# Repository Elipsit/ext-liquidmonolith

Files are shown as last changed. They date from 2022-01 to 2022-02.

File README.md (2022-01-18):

# ext-liquidmonolith
**Burning Man 2022; Project Liquid Monolith**
## Project Description
The Liquid Monolith invites participants to see the world through different lenses, by presenting them with a fluid moving display that resembles "Rorschach Inkblot Tests" that helps us unravel their dreams.<br/>

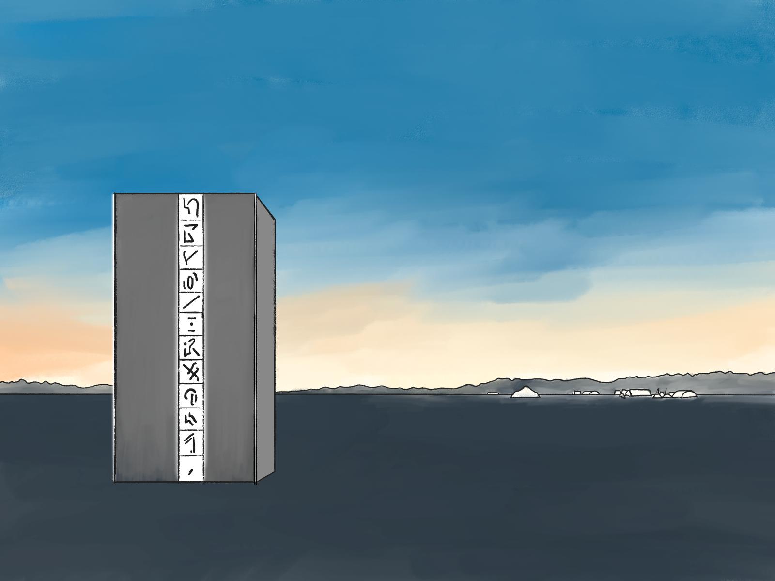
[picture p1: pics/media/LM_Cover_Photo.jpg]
LM_Cover_Photo


### Current Status
This project is in a prototype development stage<br/>

# Working Pototype
**Here is a working prototype of electromagnets sequencing the ferrofluid in the display panel:**

The 16 coil demo next to the large sample tank<br/>
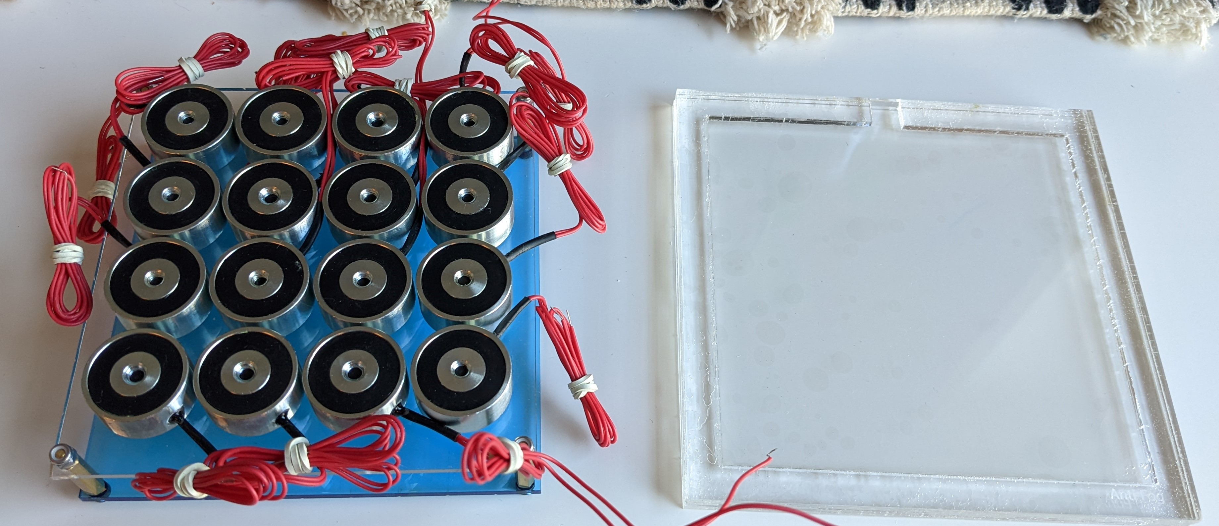
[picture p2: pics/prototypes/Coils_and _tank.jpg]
coil_and_tank


Here is a working demo<br/>

Demo_16_Array (https://www.youtube.com/watch?v=od863sYBf_k)

## Youtube Videos
**This is a link to the playlist of testing videos:**<br/>
https://youtube.com/playlist?list=PLEcu0RNHthJt5TEQliIqUSDUa66y-6SBE

# Project Research
This project was inspired from a youtube channel called [Applied Procrastination](https://www.youtube.com/watch?v=5PFgVtzsXHM)

# The Prototype

## Electrical
Several electromagnet coil topologies were tested:<br/>
Coil_options

I ordered a sample ferrofluid vial and used a custom PCB from a previous project to validate coils<br/>

Demo_single (https://www.youtube.com/watch?v=ZpuwwRlafGQ)

I chose to settle of a smaller one that was cheaper. A smaller coil required a system voltage increase from 12V to 24V to maintain the needed force.<br/>

Here is our prototype 16 coil array:<br/>

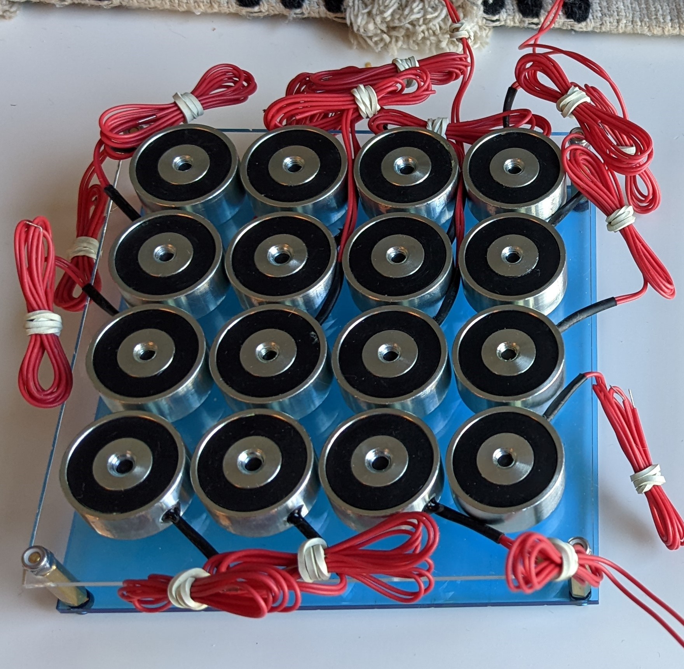
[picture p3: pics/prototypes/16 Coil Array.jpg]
16_Coil_Array

I made a custom board to test the coils <br/>

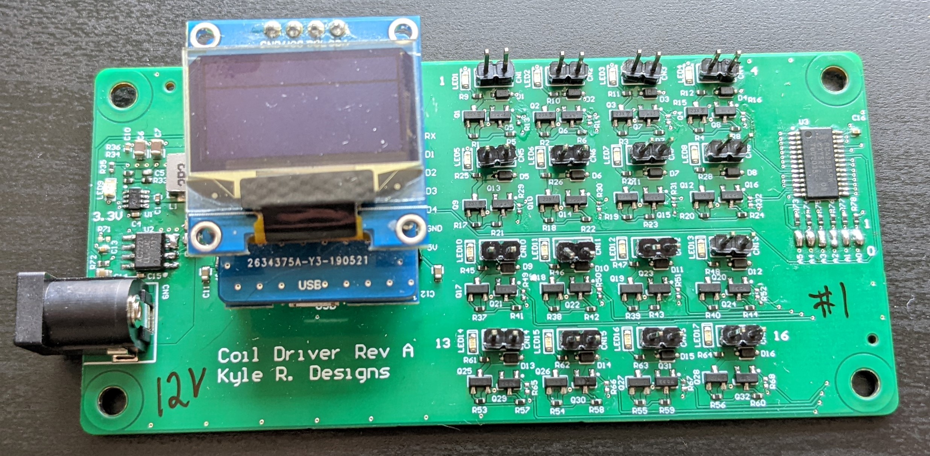
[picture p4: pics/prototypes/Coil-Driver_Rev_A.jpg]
Driver_RevA


Here is a video of the start up test:<br/>
PWM_Driver (https://www.youtube.com/watch?v=yCkvBs--dNo)

## Ferrofluid Tank

### Tank Materials

The demo video from [Applied Procrastination](https://www.youtube.com/watch?v=5PFgVtzsXHM) used glass enclosures, but I felt this would be an issue for the Playa.
I chose to research into Acrylic tanks. This was an issues since Ferrofluid is sticky and tends to coat most materials.
Research was done into anti-stick coatings.

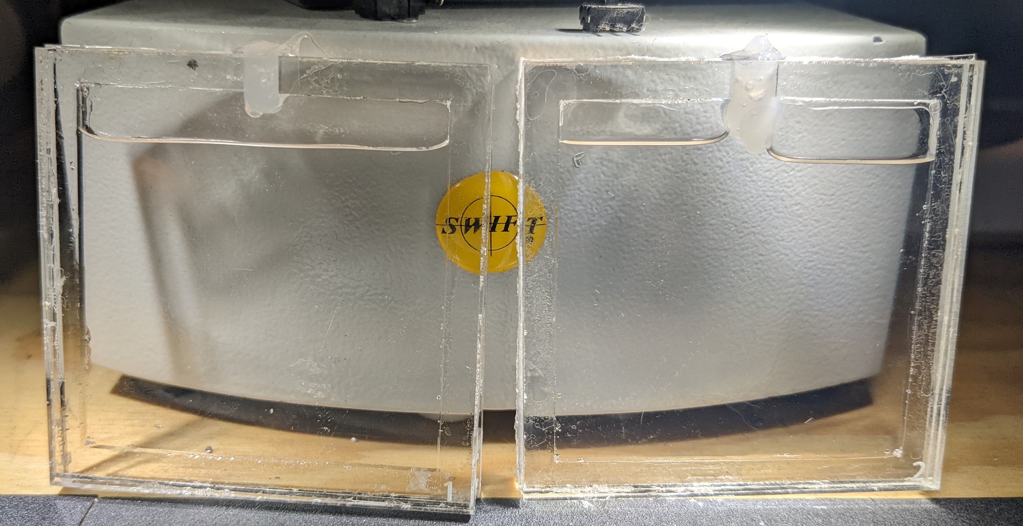
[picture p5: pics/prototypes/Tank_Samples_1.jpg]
Tank_Samples1


Some coatings perfromed better than others:<br/>

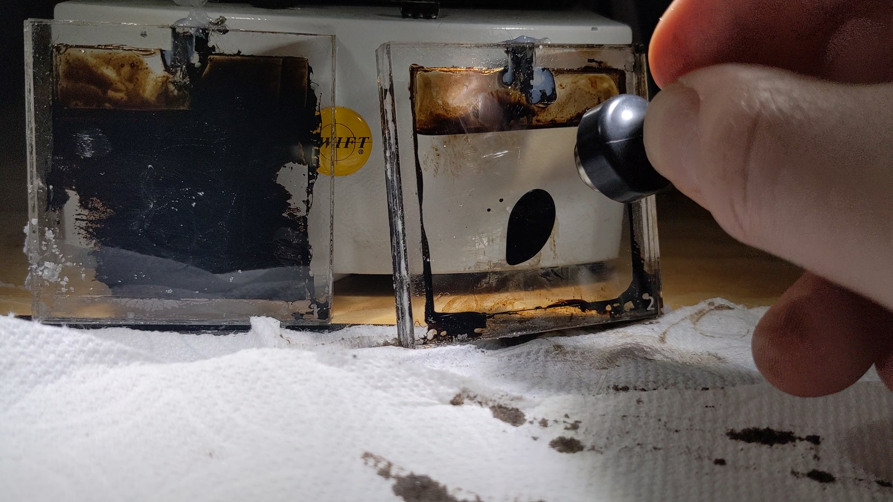
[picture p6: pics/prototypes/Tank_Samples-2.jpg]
Tank_Samples2

			
Here is a video of testing:<br/>
			
Sample_tank (https://www.youtube.com/watch?v=bsLCswysqHQ)

several glue and epoxy options were tested before a water tight solution was found:<br/>

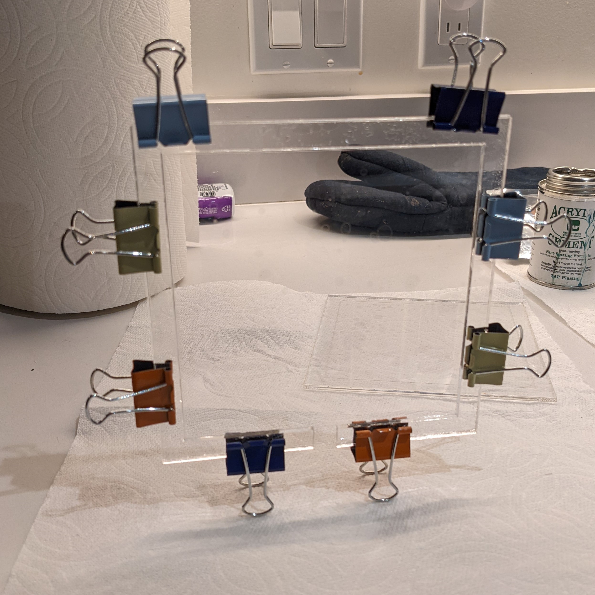
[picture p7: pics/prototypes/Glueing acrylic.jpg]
gluing


When I was able to build one that perfromed as well as the glass ones I scaled the size to fit the 16 electromagnet demo<br/>

large-tank

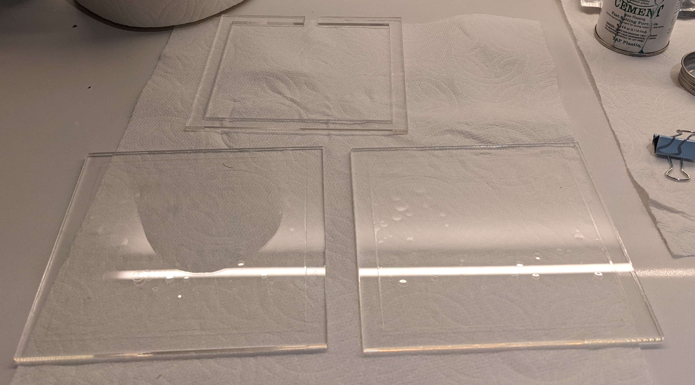
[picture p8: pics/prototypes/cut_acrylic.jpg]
Cut_Acrylic


Here is the completed tank<br/>

Completed_large_tank

Here is a Video:<br/>
Demo_Tank (https://www.youtube.com/watch?v=9LUUrNeGJJY)

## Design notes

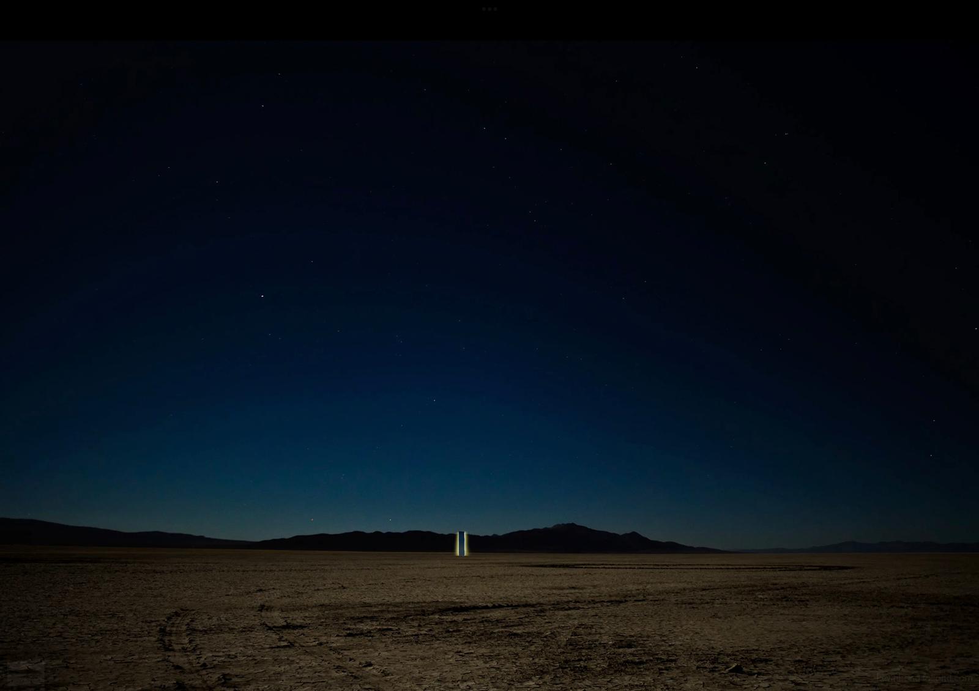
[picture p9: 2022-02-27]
pics/media/WhatsApp Image 2022-01-17 at 5.41.11 PM.jpeg

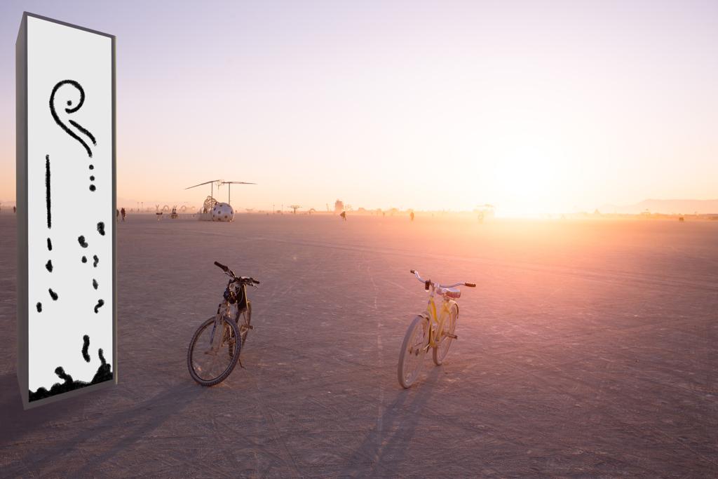
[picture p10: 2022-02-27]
pics/media/LM_Day.jpeg

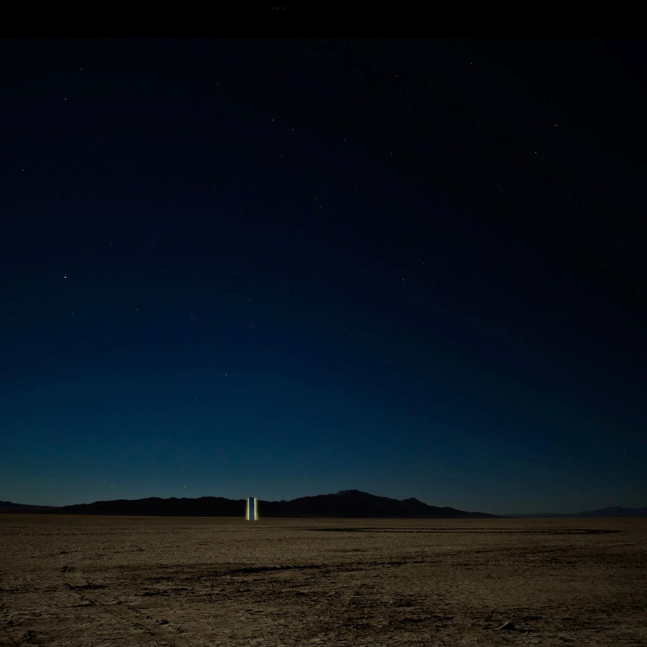
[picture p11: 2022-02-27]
pics/media/WhatsApp Image 2022-01-17 at 5.41.17 PM.jpeg

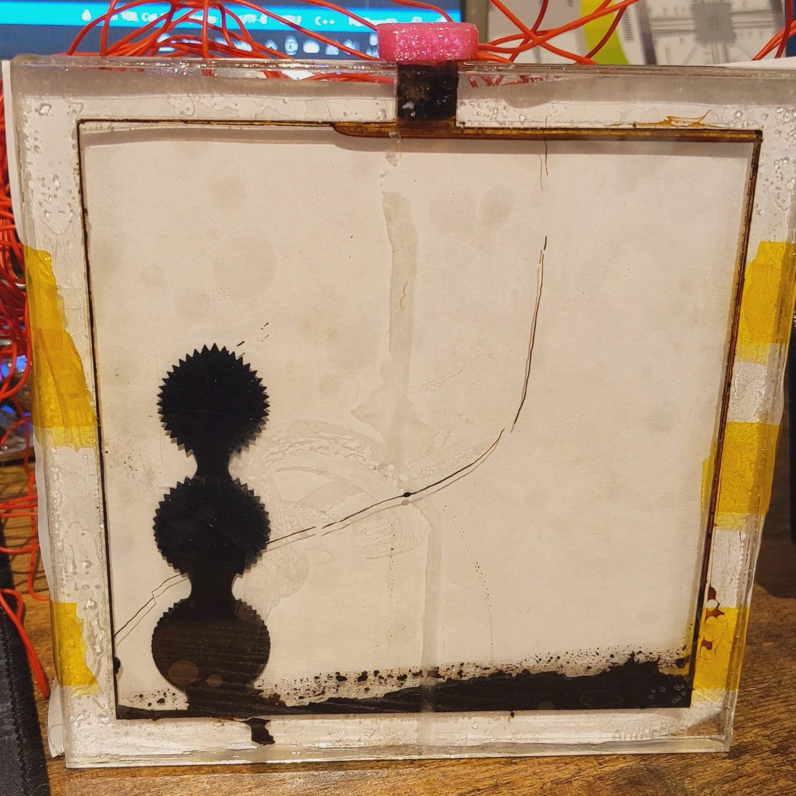
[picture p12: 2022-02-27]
pics/prototypes/3Coil-demo.jpg

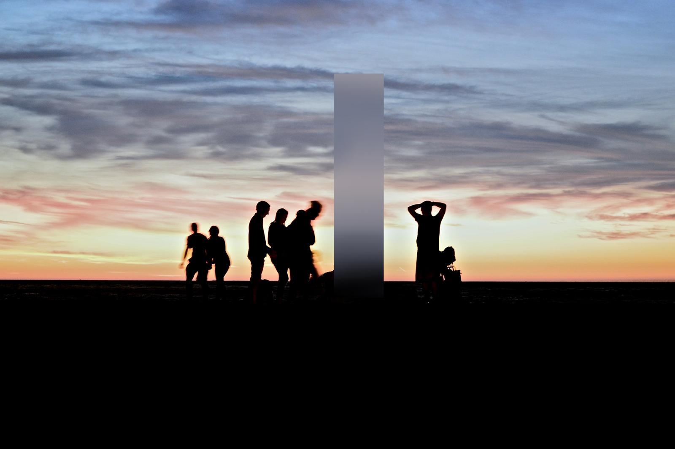
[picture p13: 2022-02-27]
pics/media/LM_Sunset.jpeg

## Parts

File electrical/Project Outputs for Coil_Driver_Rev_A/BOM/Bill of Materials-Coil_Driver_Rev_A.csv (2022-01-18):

Description | Designator | Footprint | Quantity | Manufacturer 1 | Manufacturer Part Number 1 | Supplier 1 | Supplier Part Number 1
±10% 16V Ceramic Capacitor X5R 0402 (1005 Metric) | C1, C4, C10 | CAPC0402(1005)_L | 3 | Murata | GRM155R61H104KE19D | Digi-Key | 490-11917-1-ND
4.99K 0402 | R69, R70 | RESC0402(1005)_N | 2 | Panasonic | ERJ-2RKF4991X | Digi-Key | P4.99KLCT-ND
10 kOhms ±0.1% 0.063W, 1/16W Chip Resistor 0402 (1005 Metric) Automotive AEC-Q200 Thin Film | R1, R2, R3, R4, R5, R6, R7, R8, R13, R14, R15, R16, R17, R18, R19, R20, R21, R22, R23, R24, R29, R30, R31, R32, R37, R38, R39, R40, R41, R42, R43, R44, R49, R50, R51, R52, R53, R54, R55, R56, R57, R58, R59, R60, R65, R66, R67, R68, R73, R74, R75, R76, R77, R78 | RESC0402(1005)_L | 54 | Stackpole Electronics | RNCF0402BTE10K0 | Digi-Key | RNCF0402BTE10K0CT-ND
10µF ±10% 10V Ceramic Capacitor X7R 0805 (2012 Metric) | C2, C3, C6, C7 | CAPC0805(2012)_L | 4 | Murata | GRM21BR71A106KA73K | Digi-Key | 490-14381-1-ND
47pF ±5% 25V Ceramic Capacitor C0G, NP0 0402 (1005 Metric) | C5 | CAPC0402(1005)_L | 1 | KEMET | C0402C470J3GACTU | Digi-Key | 399-C0402C470J3GAC7867CT-ND
90.9 kOhms ±1% 0.063W, 1/16W Chip Resistor 0402 (1005 Metric) Automotive AEC-Q200 Thick Film | R33 | RESC0402(1005)_L | 1 | Stackpole Electronics | RMCF0402FT90K9 | Digi-Key | RMCF0402FT90K9CT-ND
CAP CER 0.1UF 16v X7R 0402 | C15, C16 | CAPC0402(1005)_L | 2 | Taiyo Yuden | EMK105BJ104KV-F | Digi-Key | 587-1226-1-ND
CAP CER 4.7uF 16V X5R 0603 | C11, C12 | CAPC0603(1608)_L | 2 | TDK | C1608X5R1C475K080AC | Digi-Key | 445-7478-1-ND
CAP CER 4700PF 50V X7R 0402 | C13 | CAPC0402(1005)_N | 1 | Murata | GRM155R71H472KA01J | Digi-Key | 490-8259-1-ND
CONN JACK R/A PCB 5.5X2.5MM | CN9 | 54-00130 | 1 | Tensility | 54-00130 | Digi-Key | 839-1513-ND
Current Sensor 5A 1 Channel Hall Effect, Differential Bidirectional | U2 | SOG.050/8A | 1 | Allegro MicroSystems | ACS725LLCTR-05AB-T
DIODE ZENER 13V 250MW SOD323 | D1, D2, D3, D4, D5, D6, D7, D8, D9, D10, D11, D12, D13, D14, D15, D16 | SOD-323 | 16 | Central Semiconductor | CMDZ5243B TR PBFREE | Digi-Key | 1514-CMDZ5243BTRPBFREECT-ND
FIXED IND 3.3UH 5A 54.7 MOHM SMD | L1 | INDP5252X30N | 1 | Vishay Dale | IHLP2020CZER3R3M01 | Digi-Key | 541-1269-1-ND
Header, 2-Pin | CN1, CN2, CN3, CN4, CN5, CN6, CN7, CN8, CN10, CN11, CN12, CN13, CN14, CN15, CN16, CN17 | HDR1X2 | 16 | TE Connectivity | 826936-2 | Digi-Key | A122912-ND
IC LED DRVR LIN DIM 25MA 28TSSOP / LED Driver 10000uA Supply Current 28-Pin TSSOP | U3 | TSOP65P640X110-28N | 1 | NXP Semiconductors | PCA9685PW
IC REG BUCK ADJ 4A TSOT23-8 | U1 | TSOT-23-8 | 1 | Richtek | RT6254AHGJ8F | Digi-Key | RT6254AHGJ8FCT-ND
LED GREEN CLEAR THIN 0603 SMD | LED1, LED2, LED3, LED4, LED5, LED6, LED7, LED8, LED10, LED11, LED12, LED13, LED14, LED15, LED16, LED17 | SM-LED-0603 | 16 | Vishay Lite-On | LTST-C191TGKT | Digi-Key | 160-1888-1-ND
LED GREEN CLEAR THIN 0603 SMD | LED9 | SM-LED-0603 | 1 | Vishay Lite-On | LTST-C191TGKT | Digi-Key | 160-1888-1-ND
MOSFET N-CH 60V 0.36A SOT-23 | Q5, Q6, Q7, Q8, Q13, Q14, Q15, Q16, Q21, Q22, Q23, Q24, Q29, Q30, Q31, Q32 | SOT23-3L | 16 | ON Semiconductor | 2V7002LT1G
MOSFET P-CH 20V 4.2A SOT23 | Q1, Q2, Q3, Q4, Q9, Q10, Q11, Q12, Q17, Q18, Q19, Q20, Q25, Q26, Q27, Q28 | DMG2305UX-7 | 16 | Rohm | RQ5C035BCTCL | Digi-Key | RQ5C035BCTCLCT-ND
PREFERRED (<3.3V): CAP CER 1UF 10V X7R 0603 | C14 | CAPC0603(1608)_L | 1 | KEMET | C0603C105K8RACTU | Digi-Key | 399-C0603C105K8RAC7867TR-ND
RES 1K OHM 1% 1/16W 0402 | R72 | RESC0402(1005)_N | 1 | Stackpole Electronics | RMCF0402FT1K00 | Digi-Key | RMCF0402FT1K00CT-ND
RES 20K OHM 1% 1/10W 0402 | R36 | RESC0402(1005)_L | 1 | Stackpole Electronics | RMCF0402FT20K0 | Digi-Key | RMCF0402FT20K0CT-ND
RES SMD 4.99K OHM 1% 1/16W 0402 | R34 | RESC0402(1005)_L | 1 | Samsung | RC1005F4991CS | Digi-Key | 1276-3468-1-ND
RES SMD 5.1K OHM 1% 1/10W 0402 | R9, R10, R11, R12, R25, R26, R27, R28, R45, R46, R47, R48, R61, R62, R63, R64 | RESC0402(1005)_L | 16 | Panasonic | ERJ-2RKF5101X | Digi-Key | P5.10KLCT-ND
RES SMD 330 OHM 1% 1/10W 0402 | R35 | RESC0402(1005)_L | 1 | Panasonic | ERJ-U02F3300X | Digi-Key | 10-ERJ-U02F3300XCT-ND
Solderable jumper for connecting things | J1, J2, J3, J4, J5, J6, J7 | RESC0603(1608)_L | 7
Wemo Mini Shield for ESP-12 | CN18 | Wemos_d1 | 1

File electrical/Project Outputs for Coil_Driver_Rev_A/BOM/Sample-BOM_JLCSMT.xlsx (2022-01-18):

Comment | Designator | Footprint | JLCPCB Part #（optional）
100uF | C1 | CAP-SMD_L3.5-W2.8 | C16133
15K | R5,R6 | R0603 | C22809
DC-005-20A_C136744 | DC1 | DC-IN-TH_DC-005-20A | C136744
Header-Female-2.54_1x8 | P2,P3 | HDR-TH_8P-P2.54-V | C27438
K2-1102DP-C4SW-04 | SW1 | KEY-TH_4P-L6.0-W6.0-P4.50-LS6.5 | C110153
ATMEGA328P-PU | U1 | DIP-28_L34.6-W7.3-P2.54-LS10.2-BL | C33901
670688000 | USB1 | USB-B-TH_67068-8000 | C114097

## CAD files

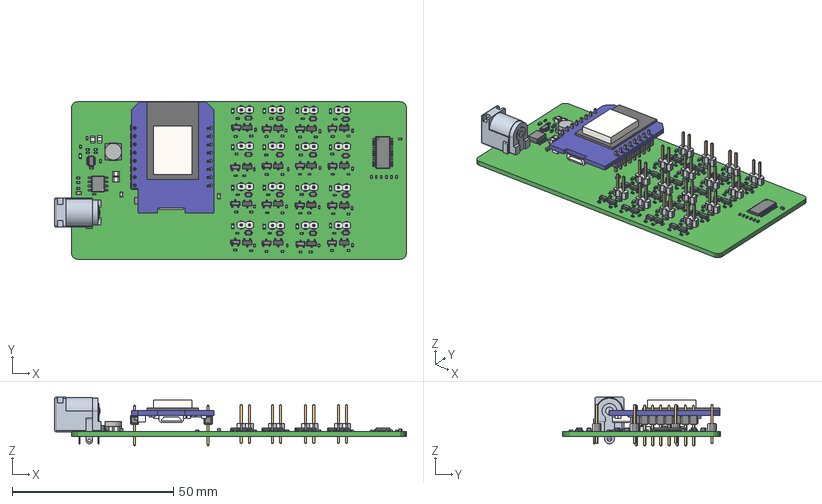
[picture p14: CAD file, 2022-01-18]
electrical/Project Outputs for Coil_Driver_Rev_A/ExportSTEP/Coil_Driver_Rev_A.step
109.1 x 48.8 x 15.2 mm
Open_CASCADE_STEP_translator_6.8_14.1
Open_CASCADE_STEP_translator_6.8_14.2.1
Leader x 36
Extruded x 267
SOIC-8D
Capacitor_0603 x 3
Open_CASCADE_STEP_translator_6.8_25.1
Open_CASCADE_STEP_translator_6.8_25.2.1
SOT-23 x 16
SW3dPS-LED_SMD0603 x 17
Open_CASCADE_STEP_translator_6.8_10.3.1 x 2
Open_CASCADE_STEP_translator_6.8_11.1.1 x 16
lead x 32
HDR1x1 x 32

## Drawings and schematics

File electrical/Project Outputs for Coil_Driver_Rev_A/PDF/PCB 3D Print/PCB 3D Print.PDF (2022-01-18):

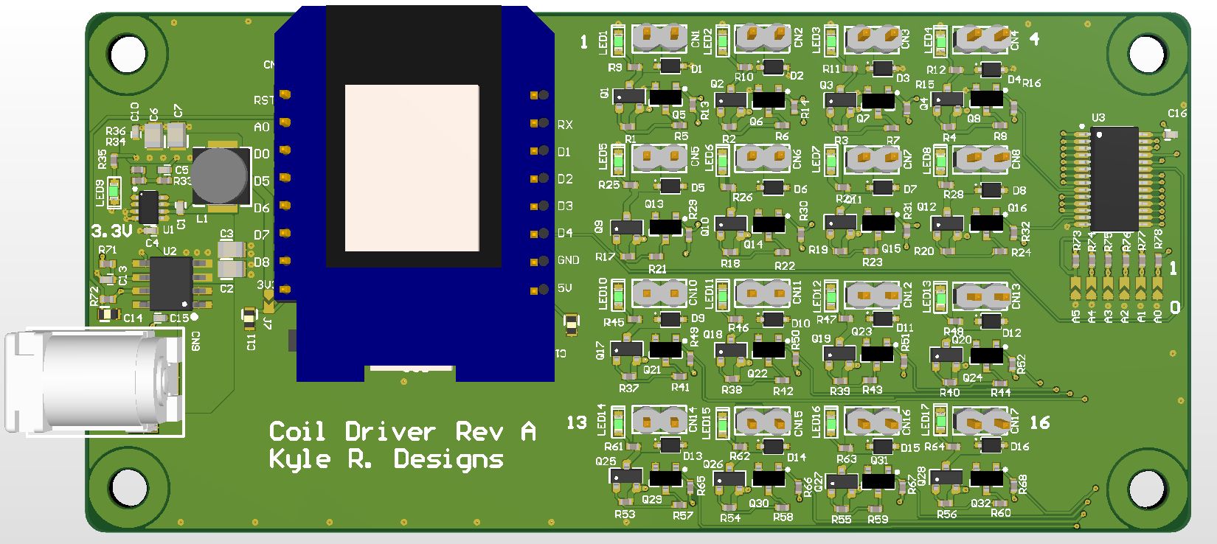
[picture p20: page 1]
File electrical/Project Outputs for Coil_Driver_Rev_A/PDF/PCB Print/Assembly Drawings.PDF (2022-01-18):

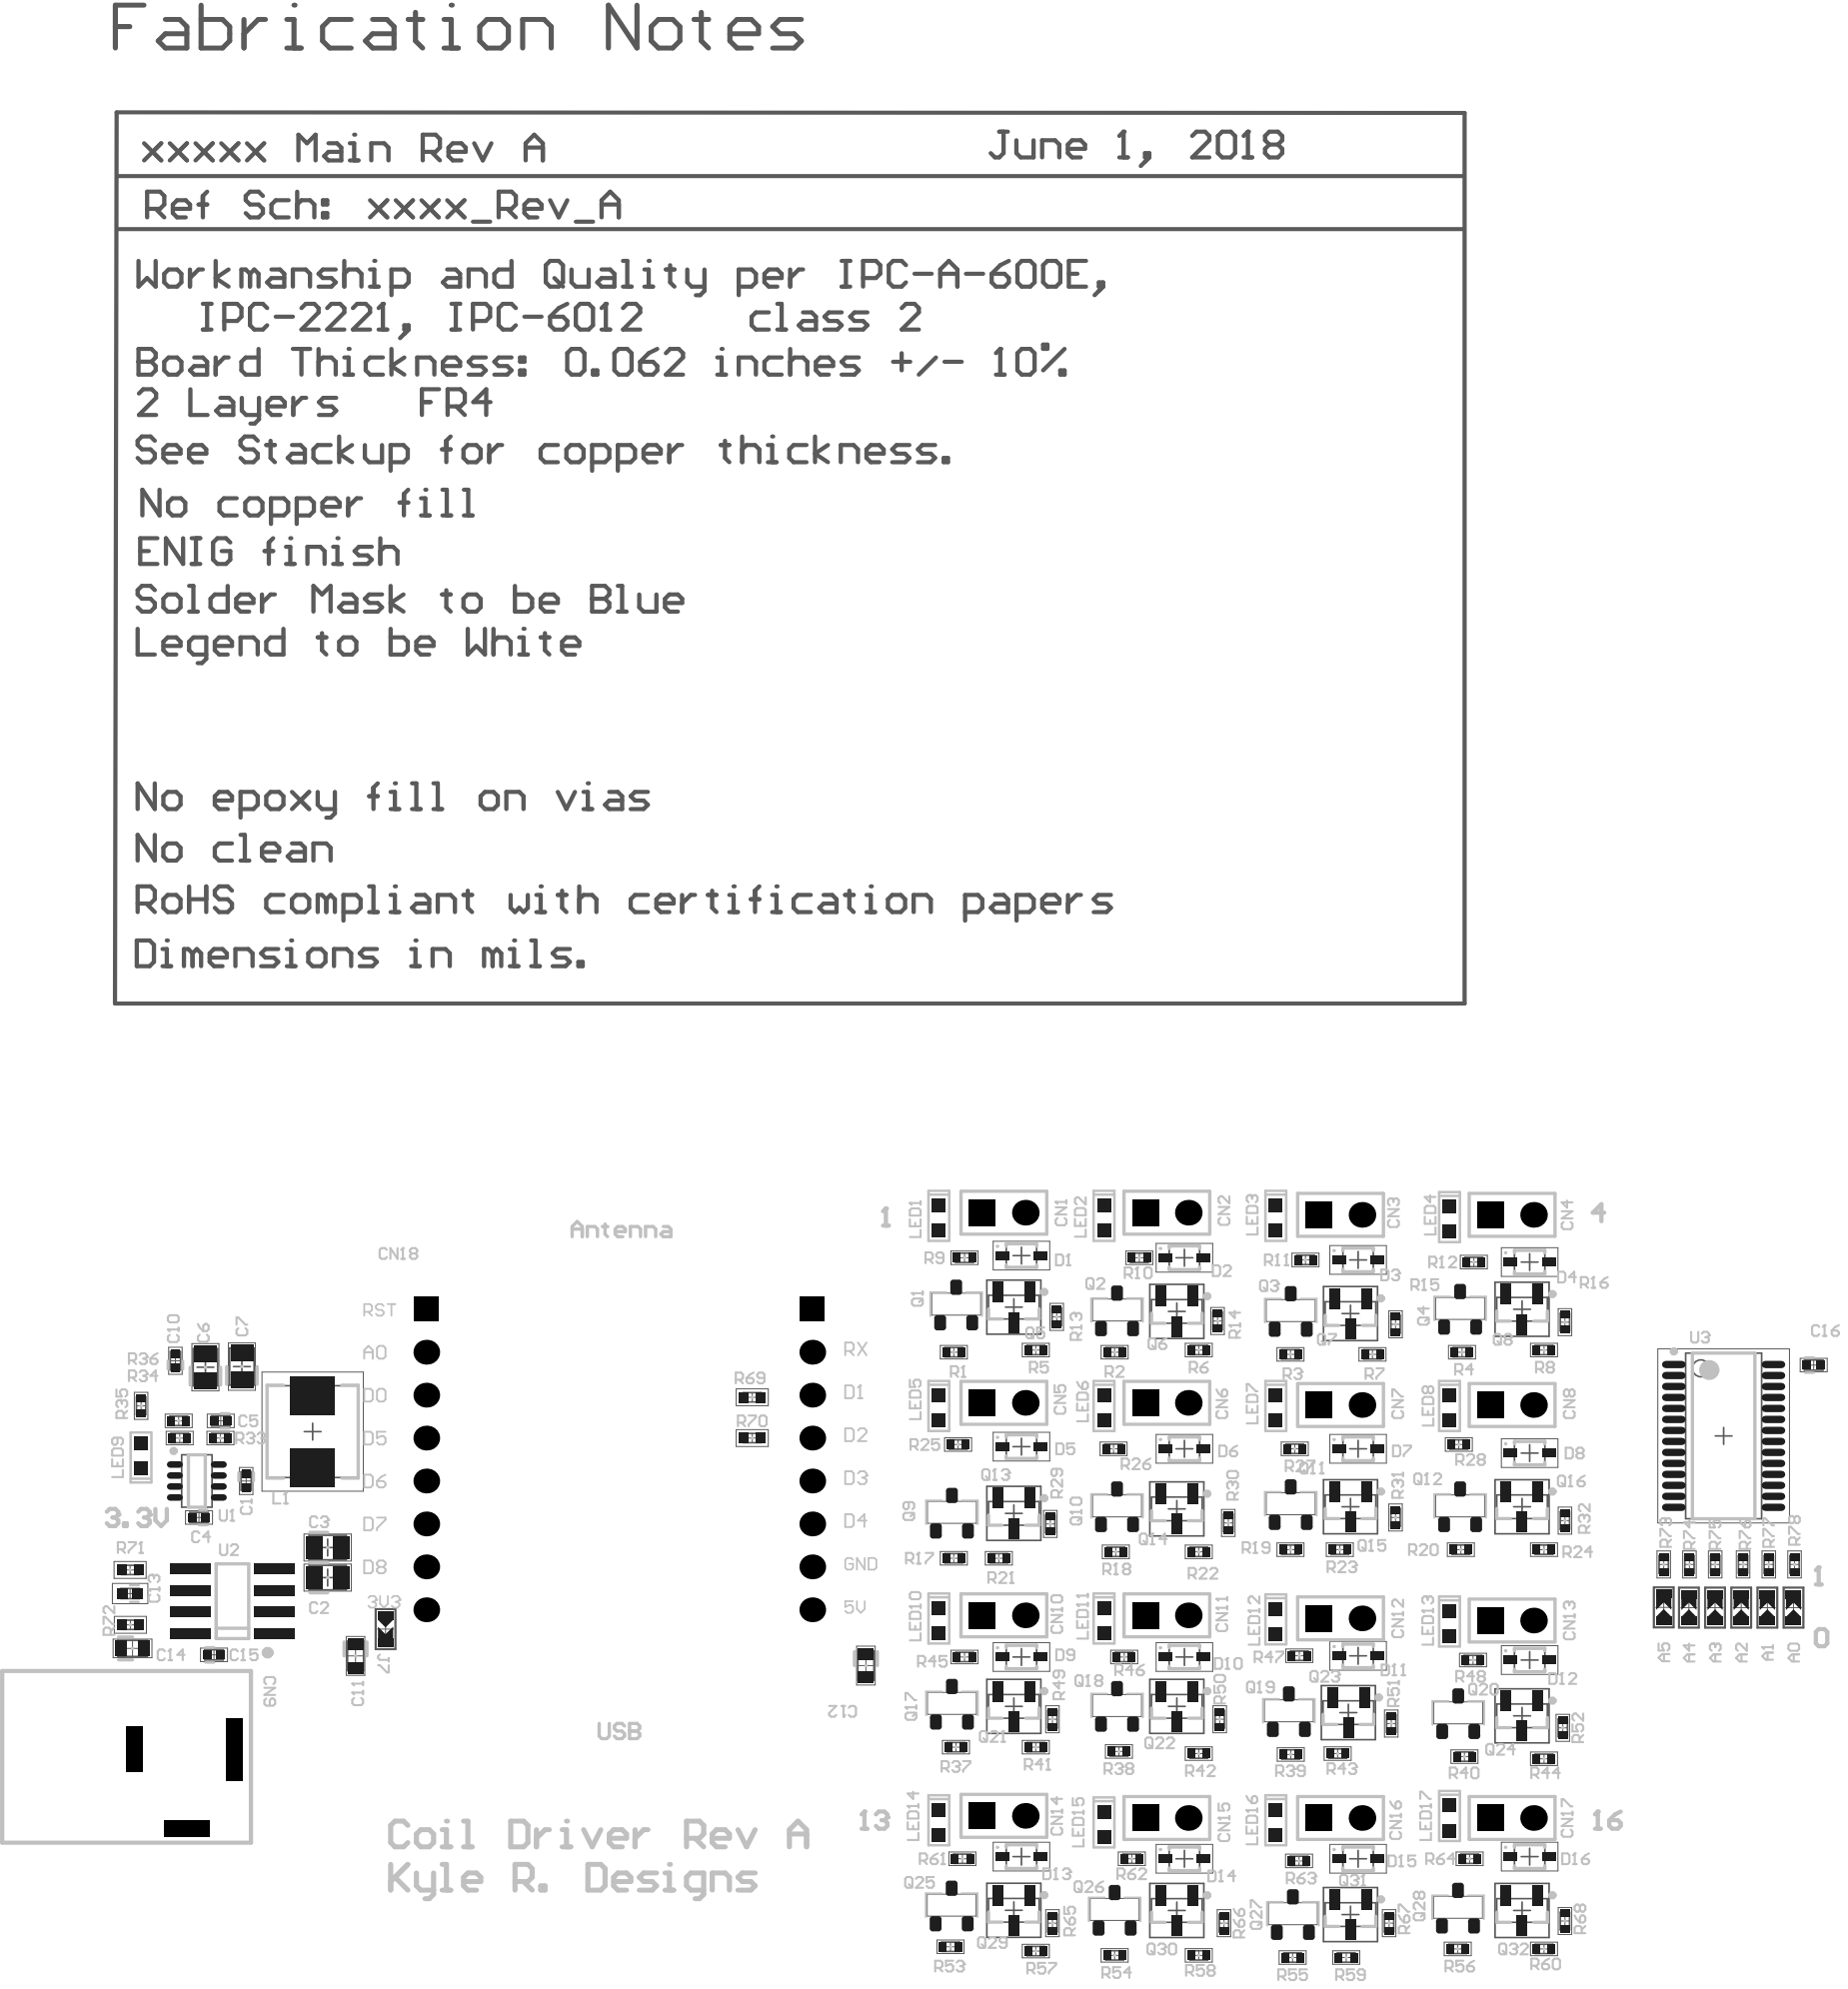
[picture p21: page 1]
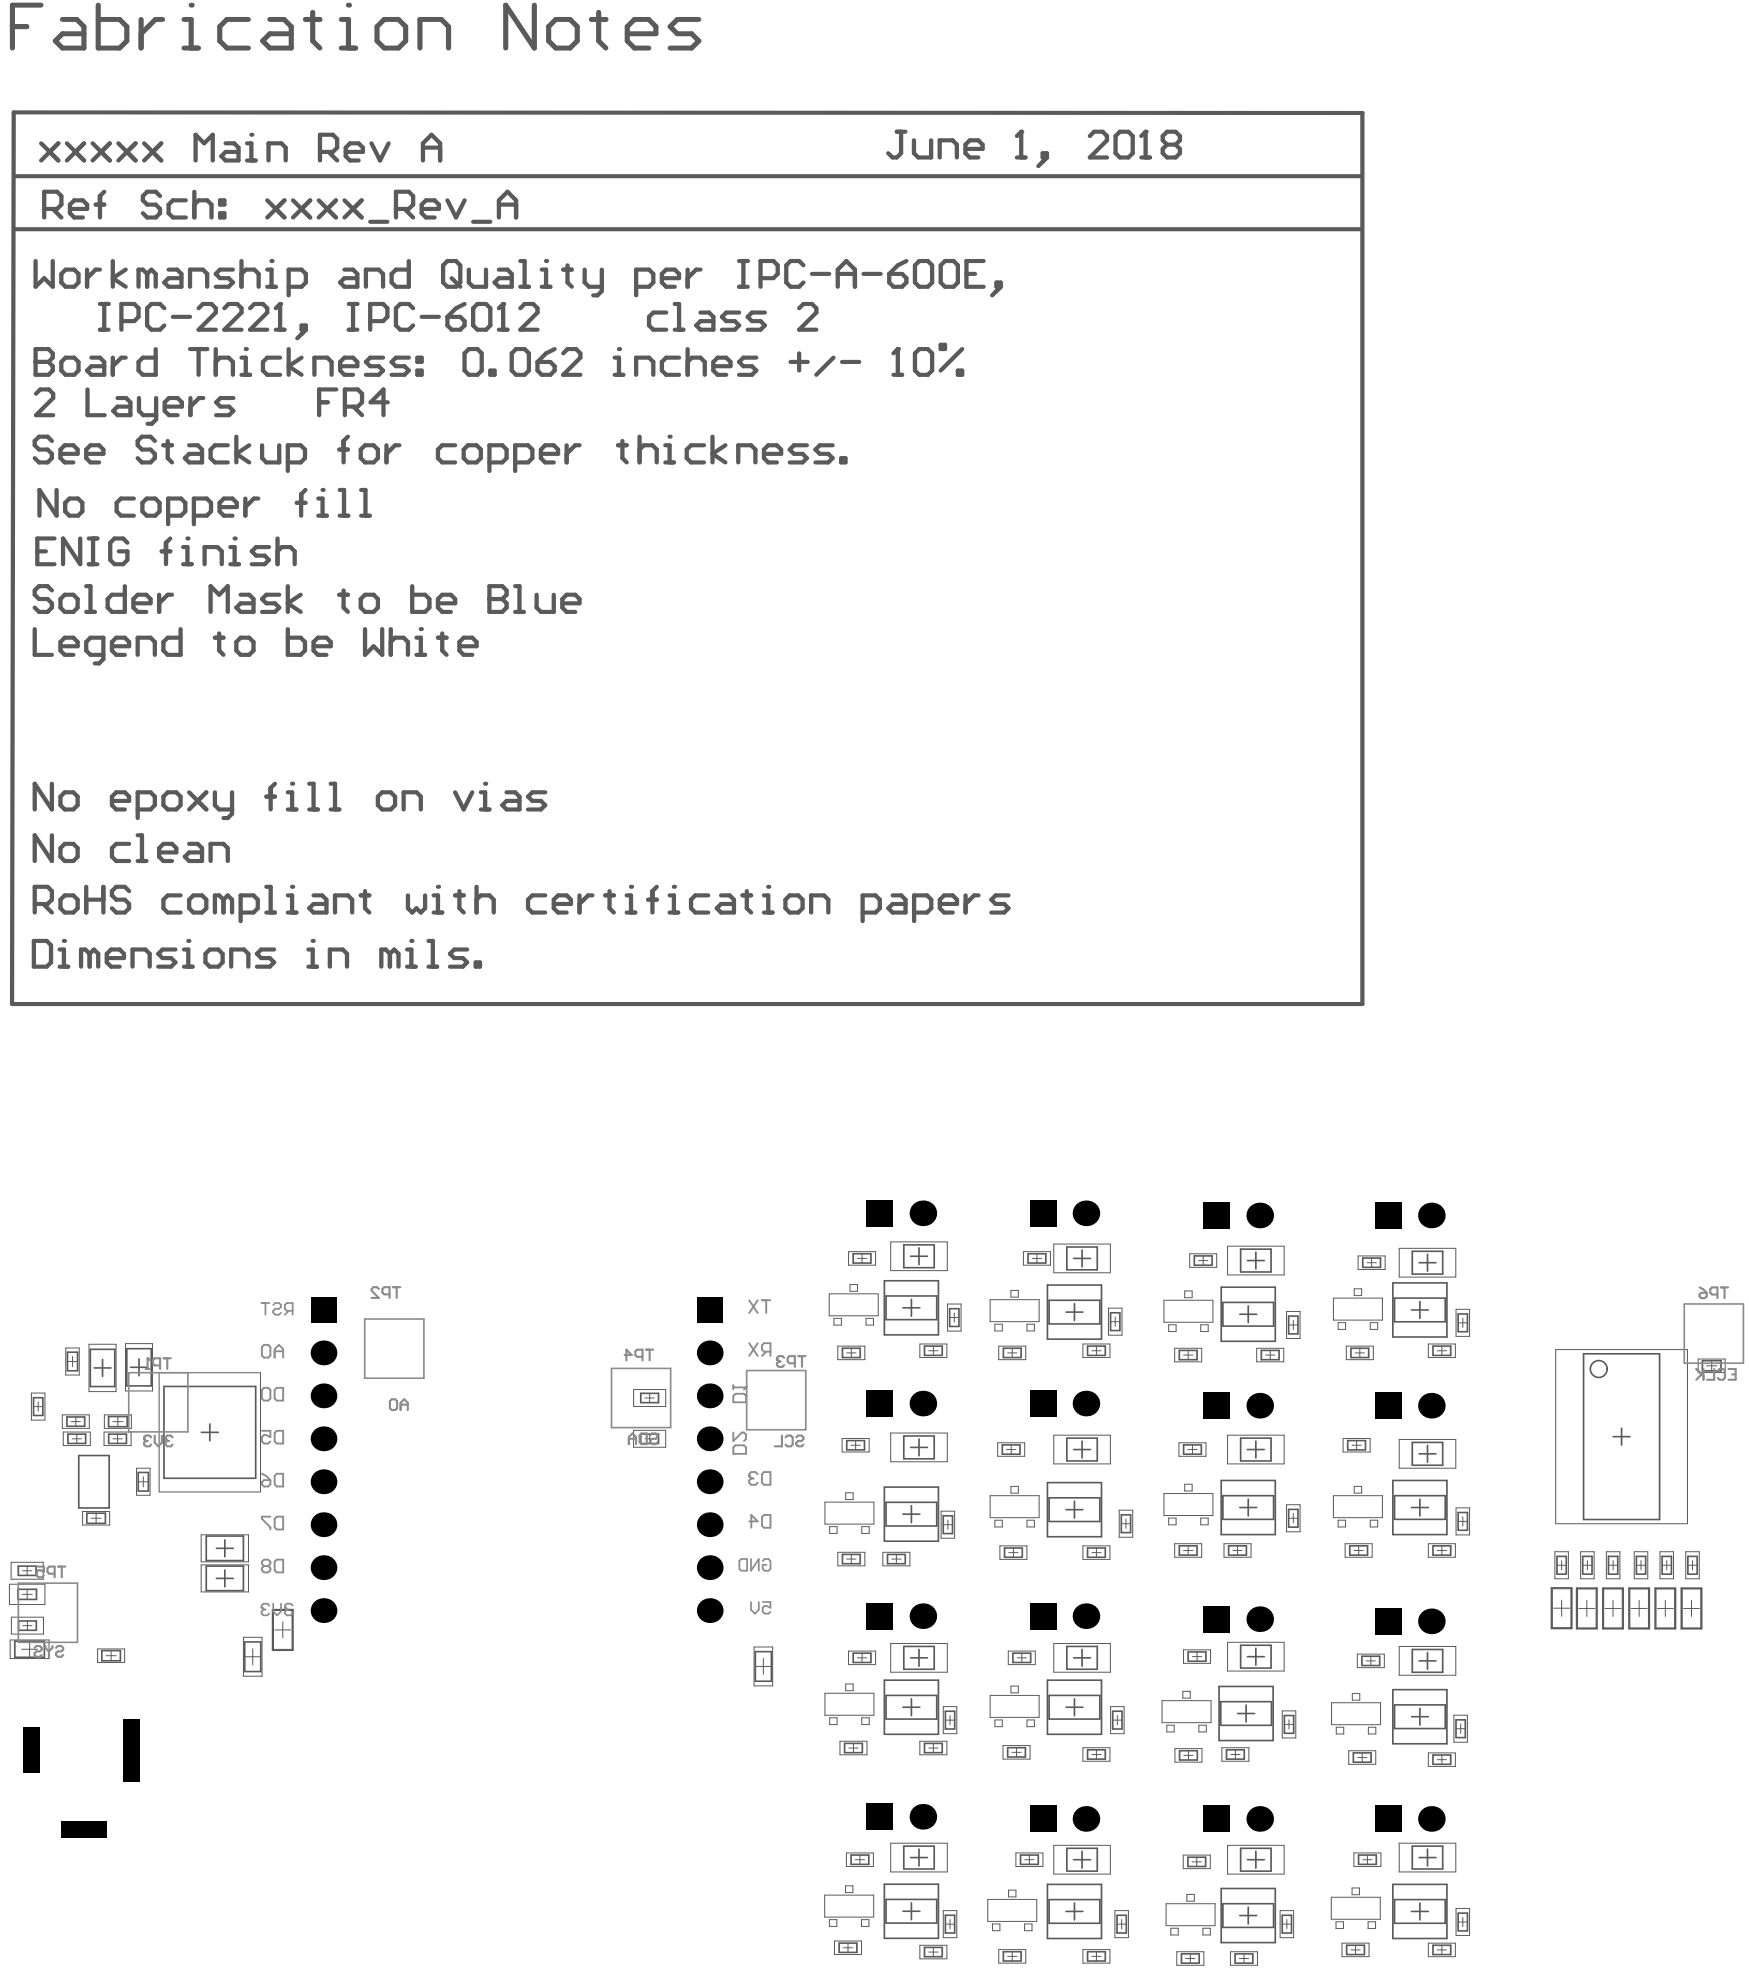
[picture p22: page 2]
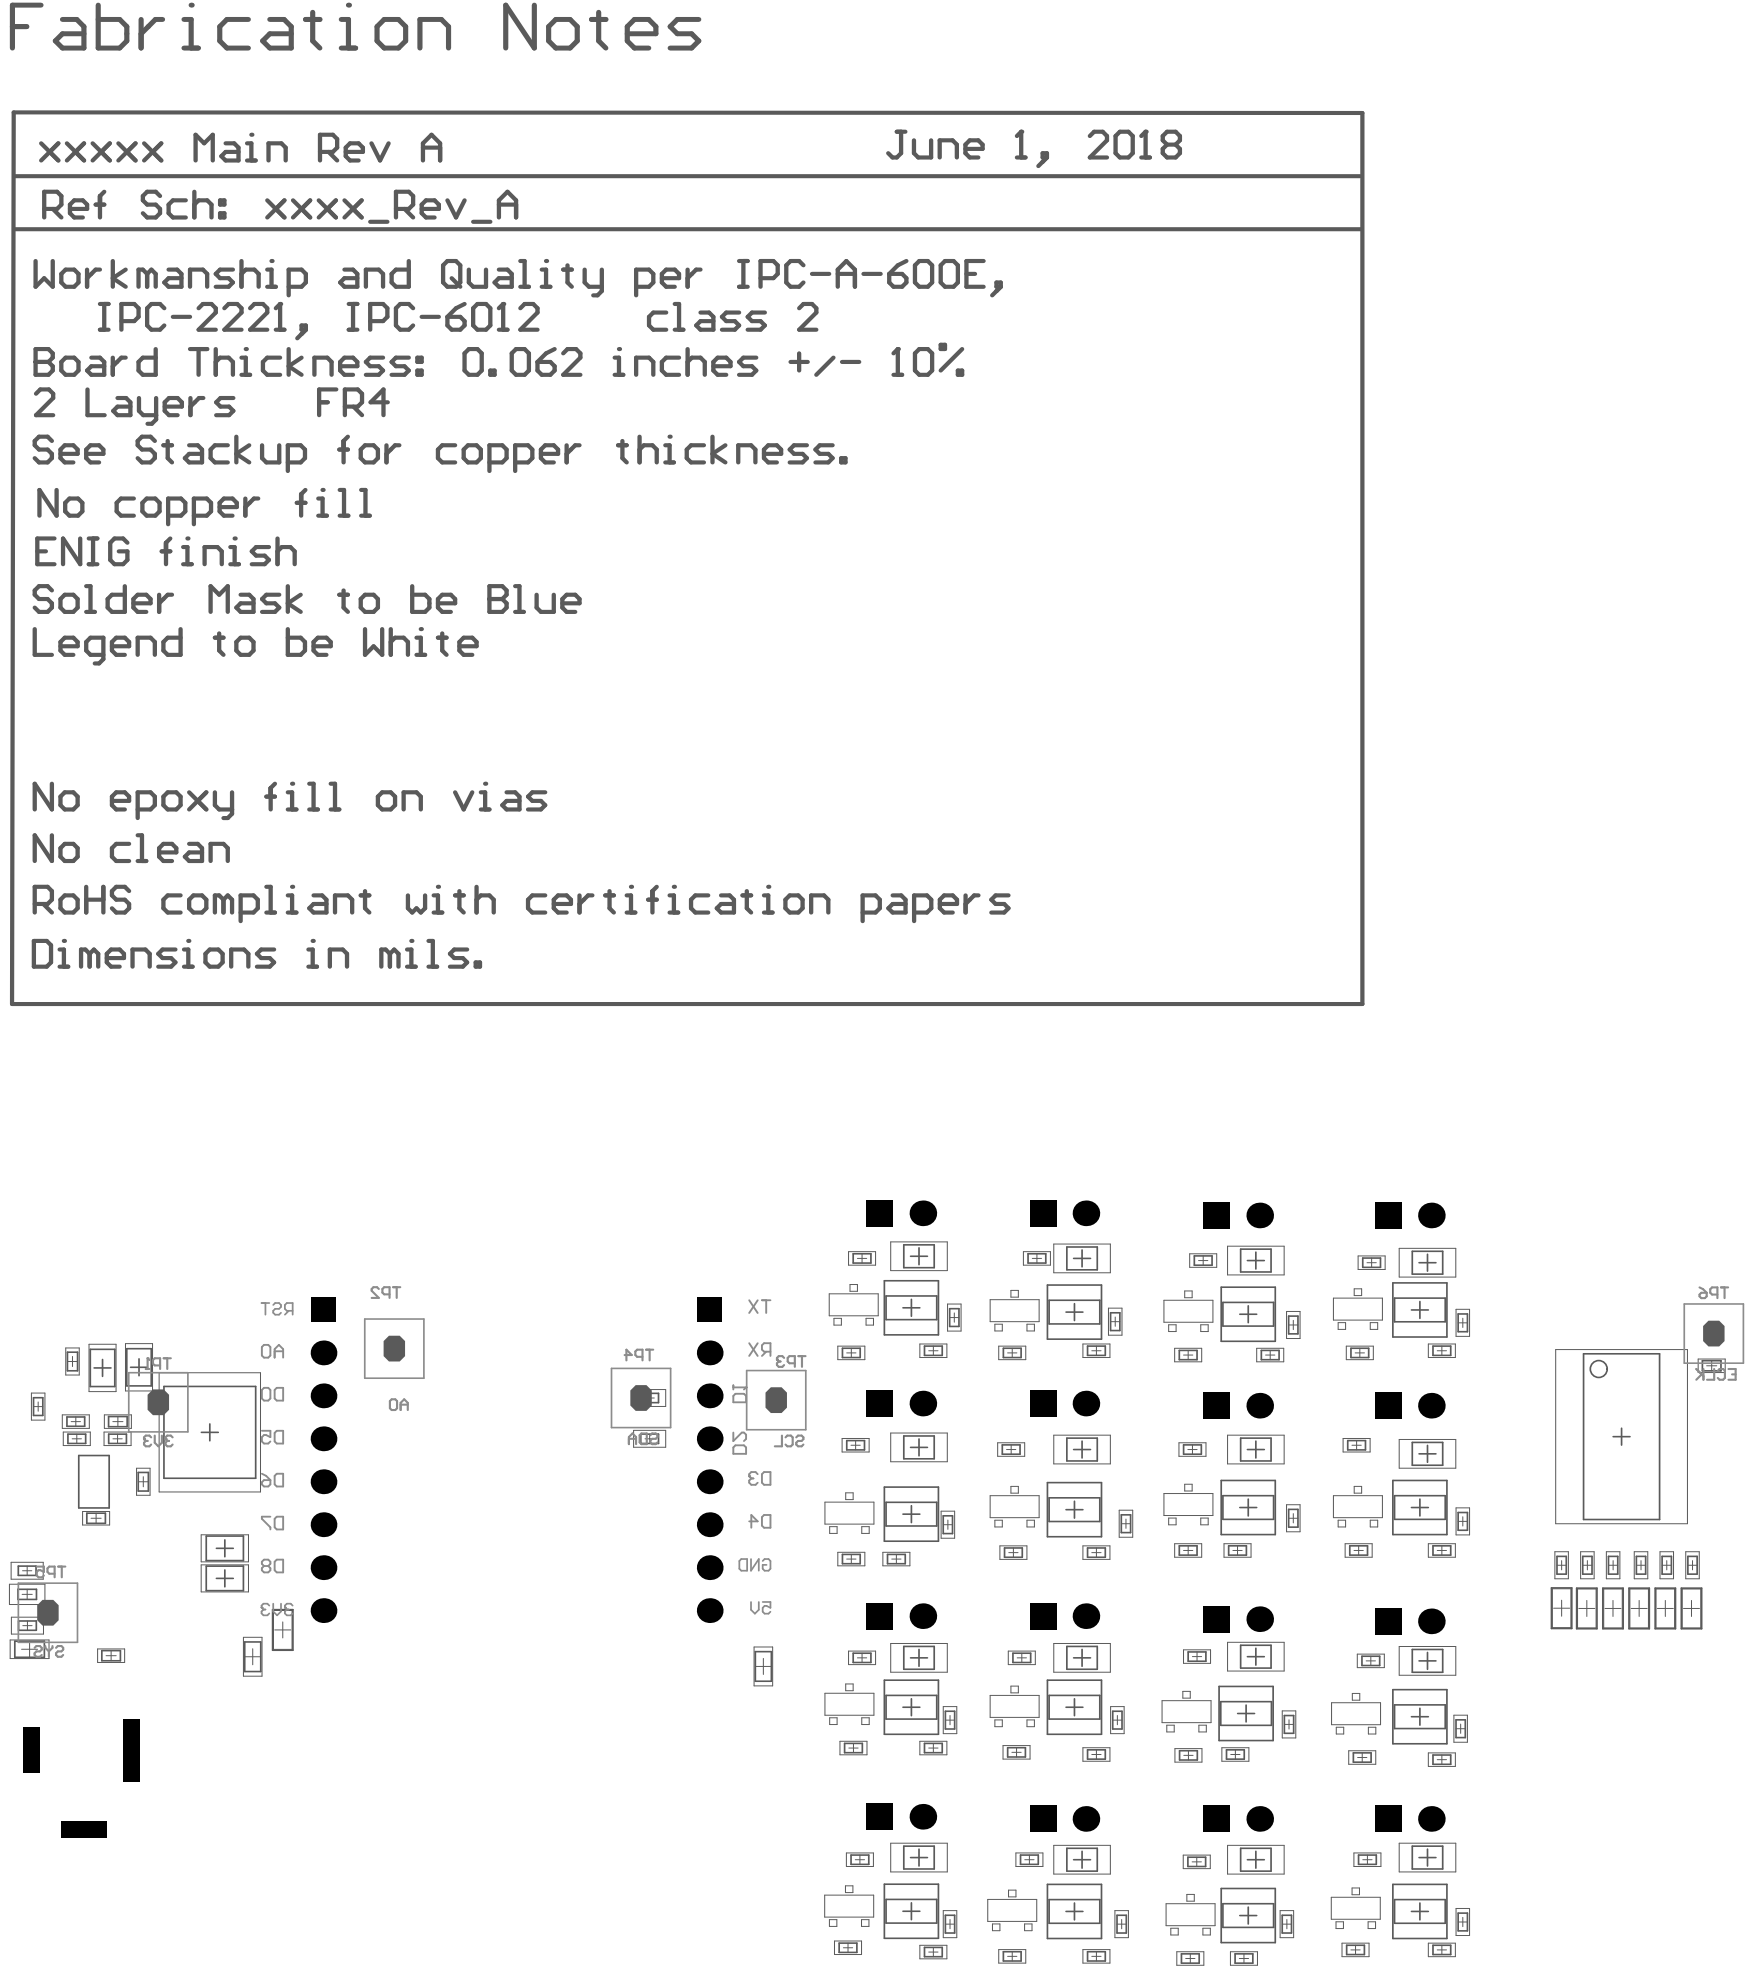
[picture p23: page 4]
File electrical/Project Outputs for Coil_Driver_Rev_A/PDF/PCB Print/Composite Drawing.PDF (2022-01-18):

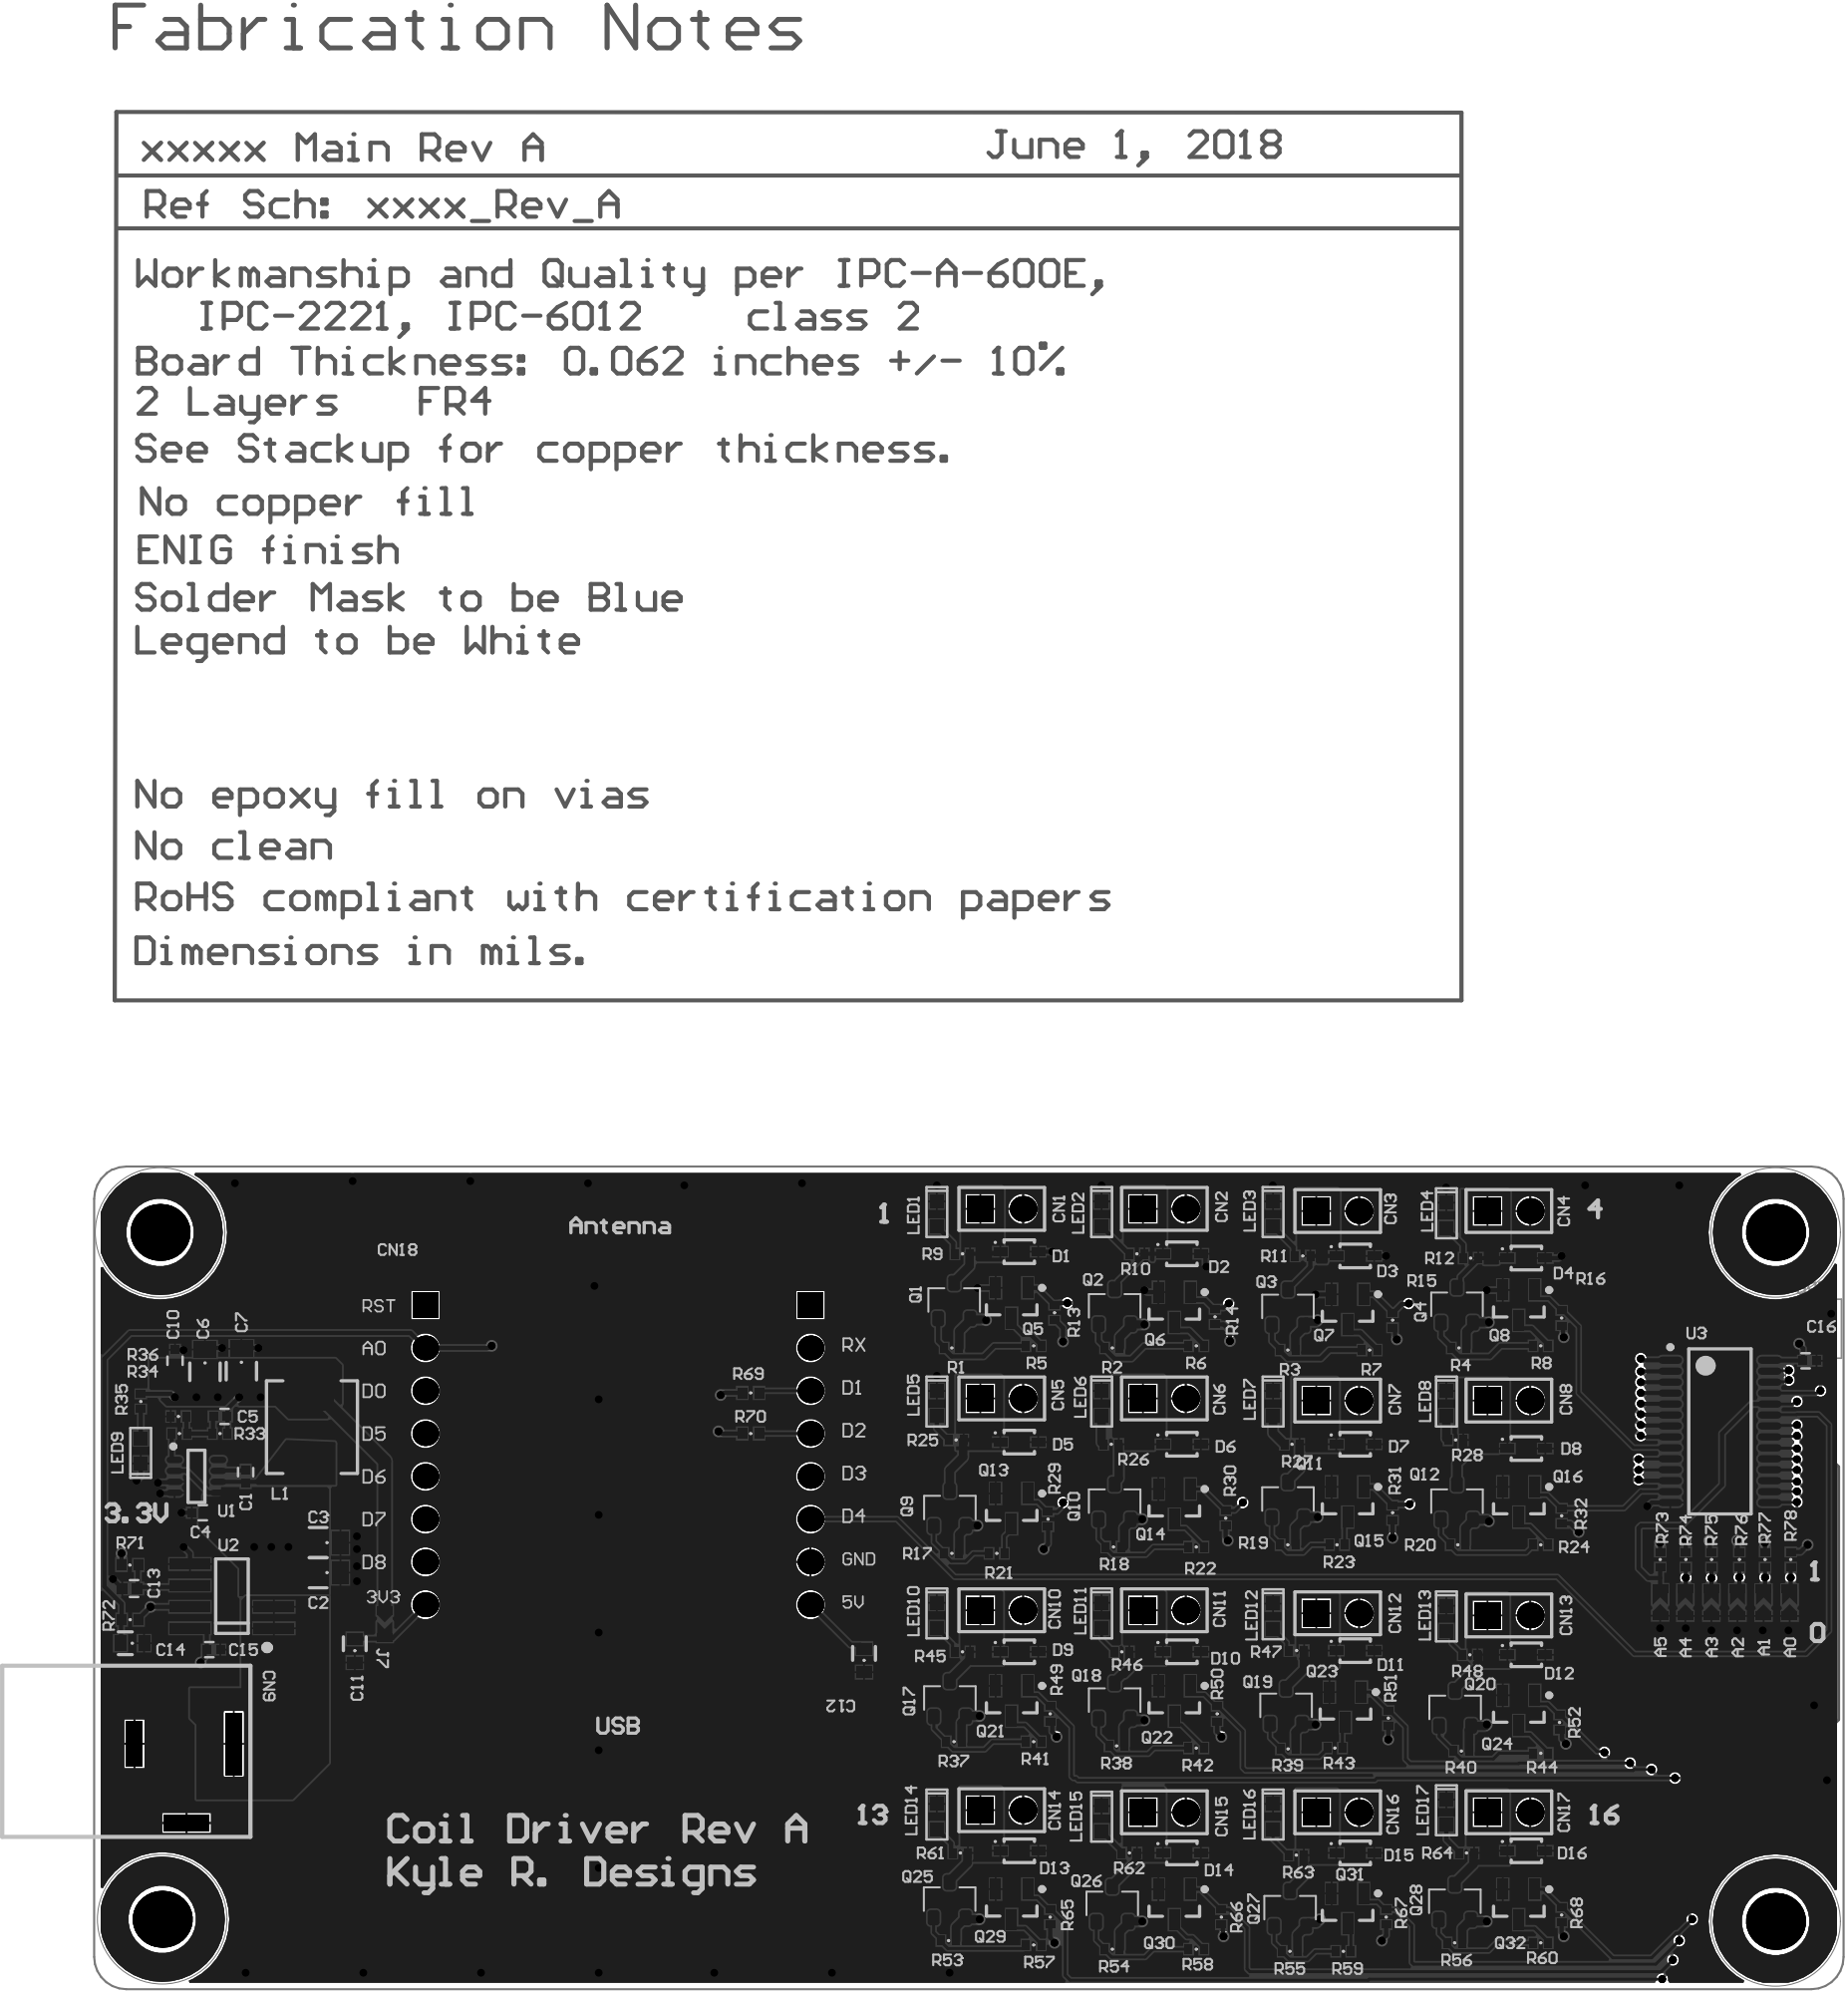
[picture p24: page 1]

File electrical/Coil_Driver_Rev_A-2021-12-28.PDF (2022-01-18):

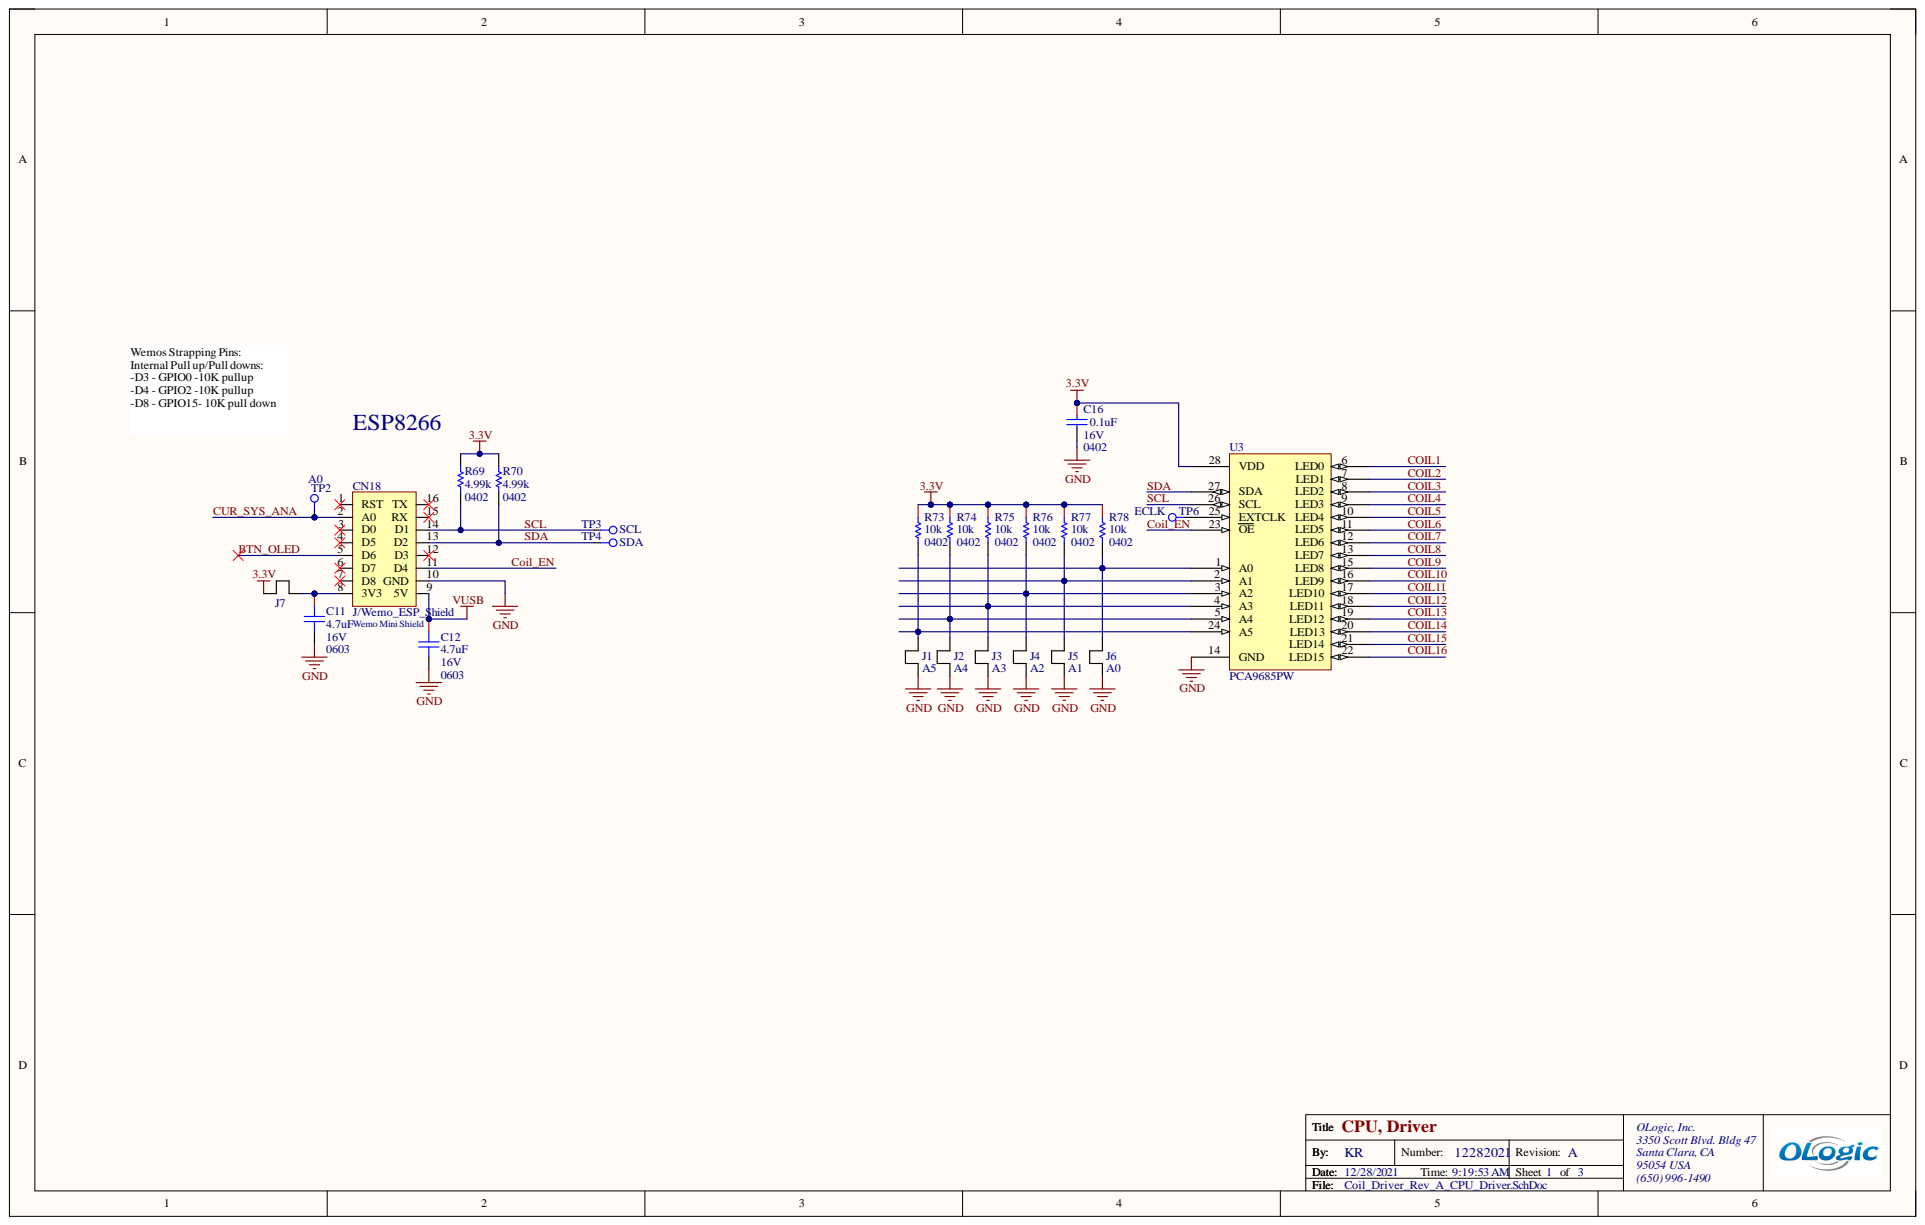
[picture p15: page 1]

Ti Ti tl tl e e CPU, Driver | OLogic, Inc . 3350 Scot t B lvd. B ldg 47 Santa C lara, CA 95054 USA (650) 996-14 90

B B y y : : KR | Numbe r : 1 2 2 8 2 0 2 | 1 Revi s i on : A
Dat Dat e e : : 12/28/ 20 2 1 Ti m e : 9:19: 53 AM | | She et 1 of 3

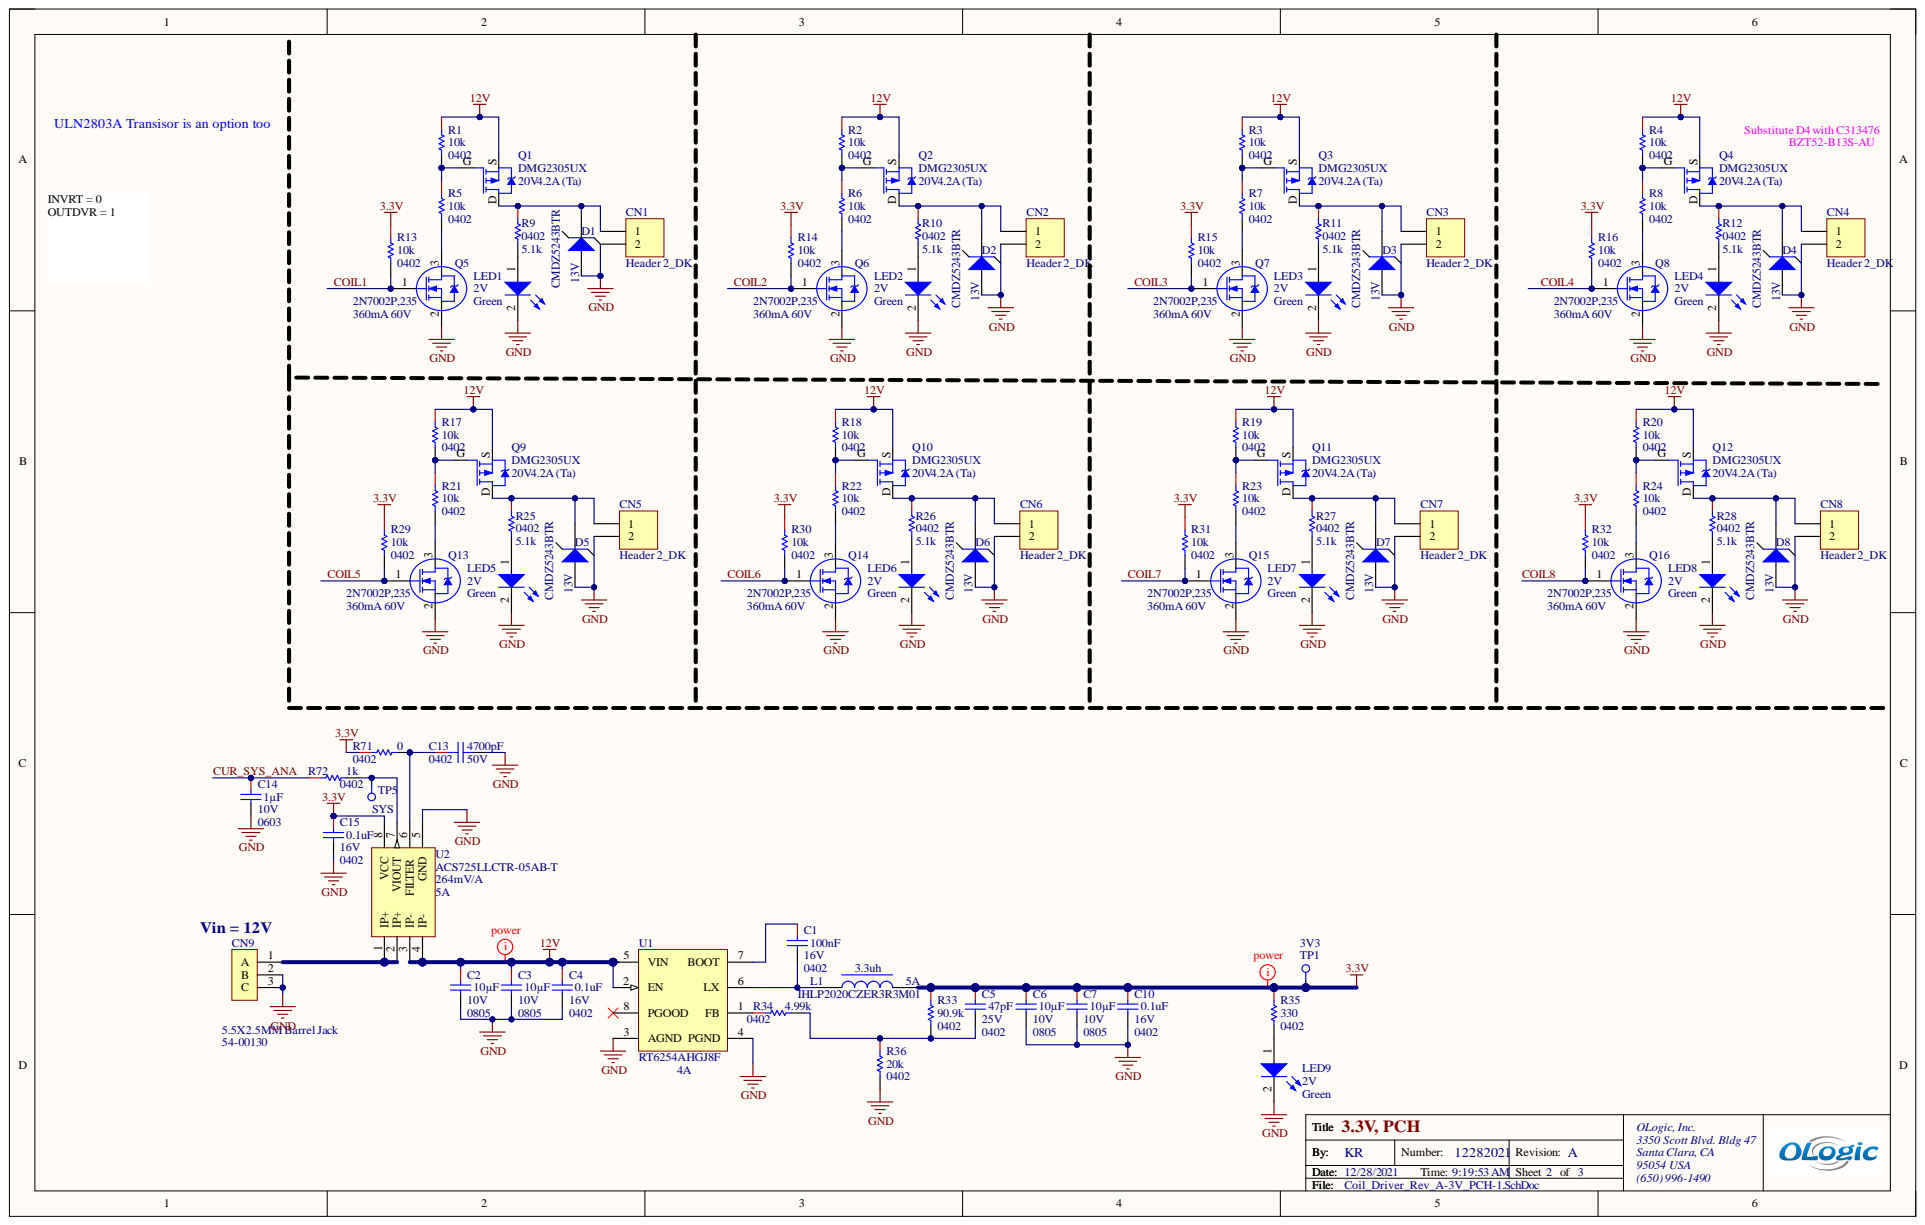
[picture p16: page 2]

ULN2803A Transisor is an option too

IP- 4 GND 5 FILTER 6 VIOUT 7 VCC 8

By: By: KR | Number: 12282021 | Revision: A
Date: Date: 12/28/2021 Time: 9:19:53 AM | | Sheet 2 of | 95054 USA 3

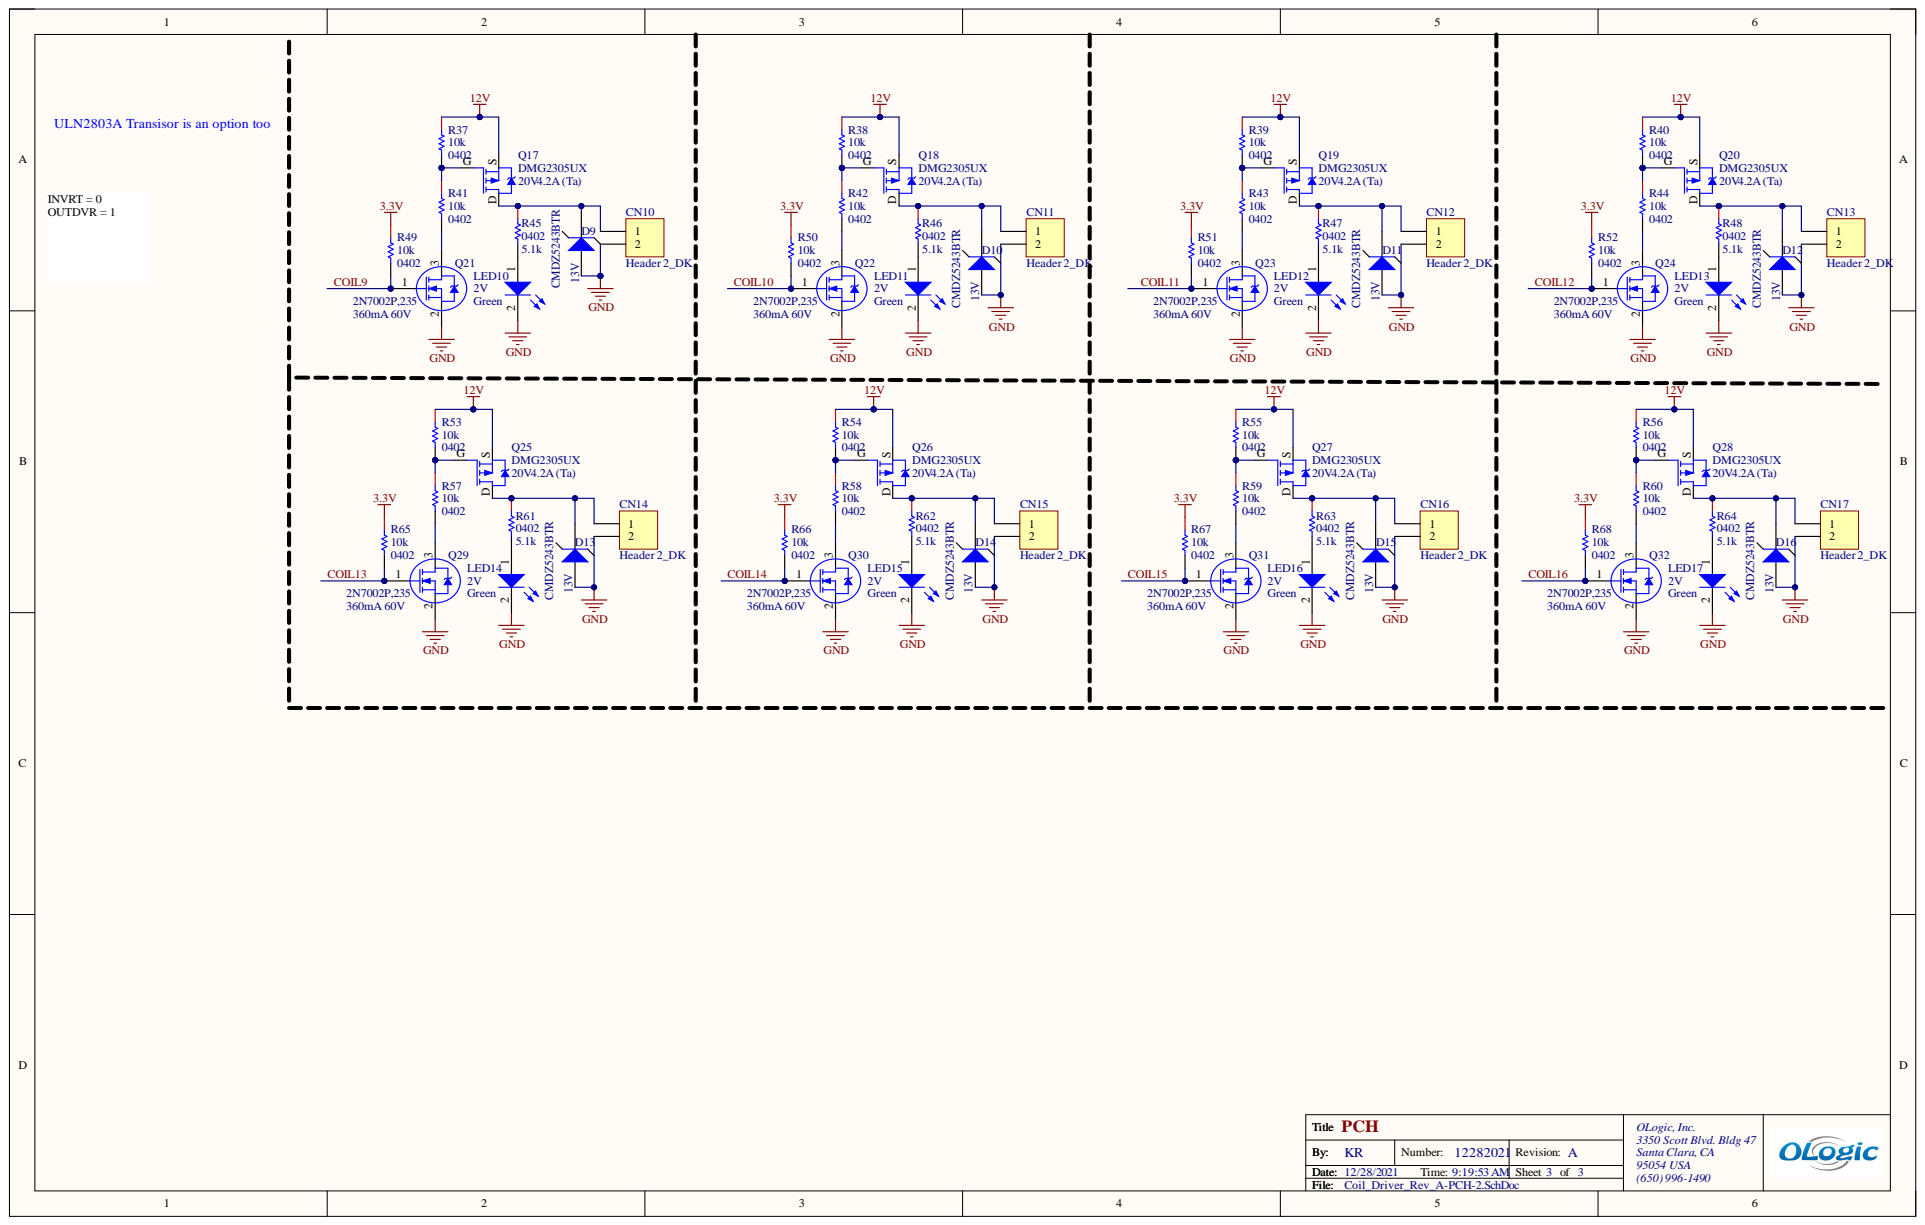
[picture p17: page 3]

Ti Ti tl tl e e PCH | OLogic, Inc . 3350 Scot t B lvd. B ldg 47 Santa C lara, CA 95054 USA (650) 996-14 90

B B y y : : KR | Numbe r : 1 2 2 8 2 0 2 | 1 Revi s i on : A
Dat Dat e e : : 12/28/ 20 2 1 Ti m e : 9:19: 53 AM | | She et 3 of 3

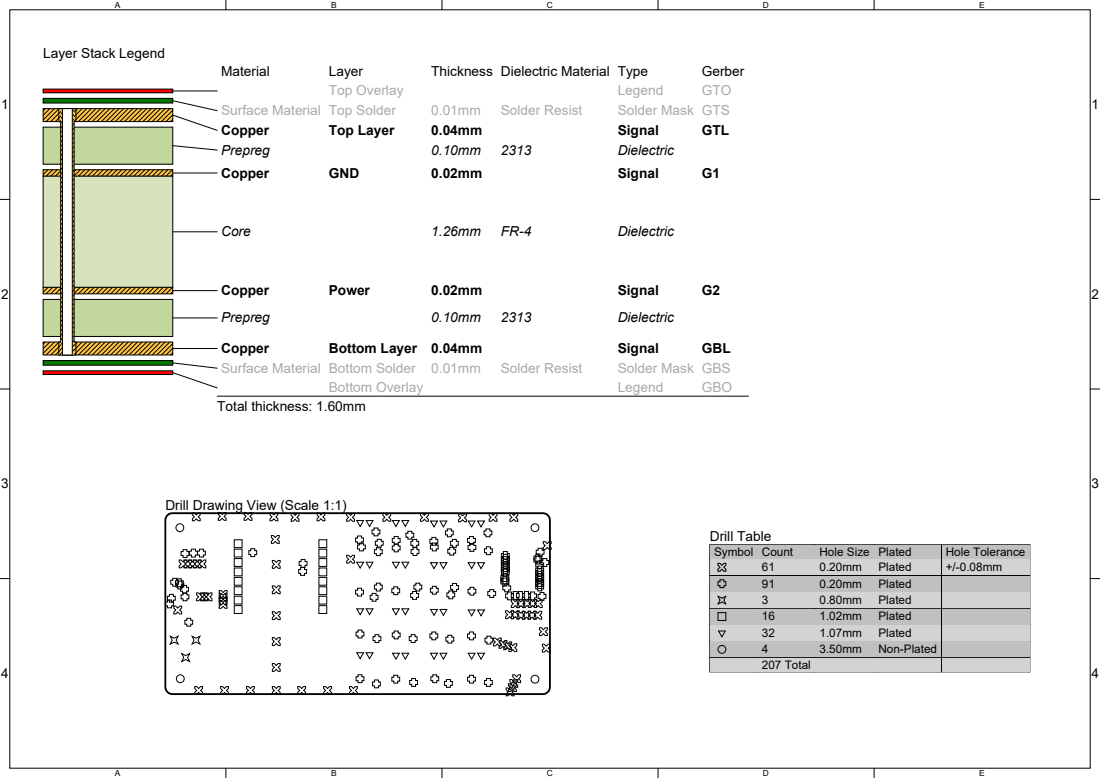
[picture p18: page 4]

Drill Drawing View (Scale 1:1)

Symbol | Count | Hole Size | Plated | Hole Tolerance

61 | 0.20mm | Plated | +/-0.08mm
91 | 0.20mm | Plated
3 | 0.80mm | Plated
16 | 1.02mm | Plated
32 | 1.07mm | Plated
4 | 3.50mm | Non-Plated
207 Total

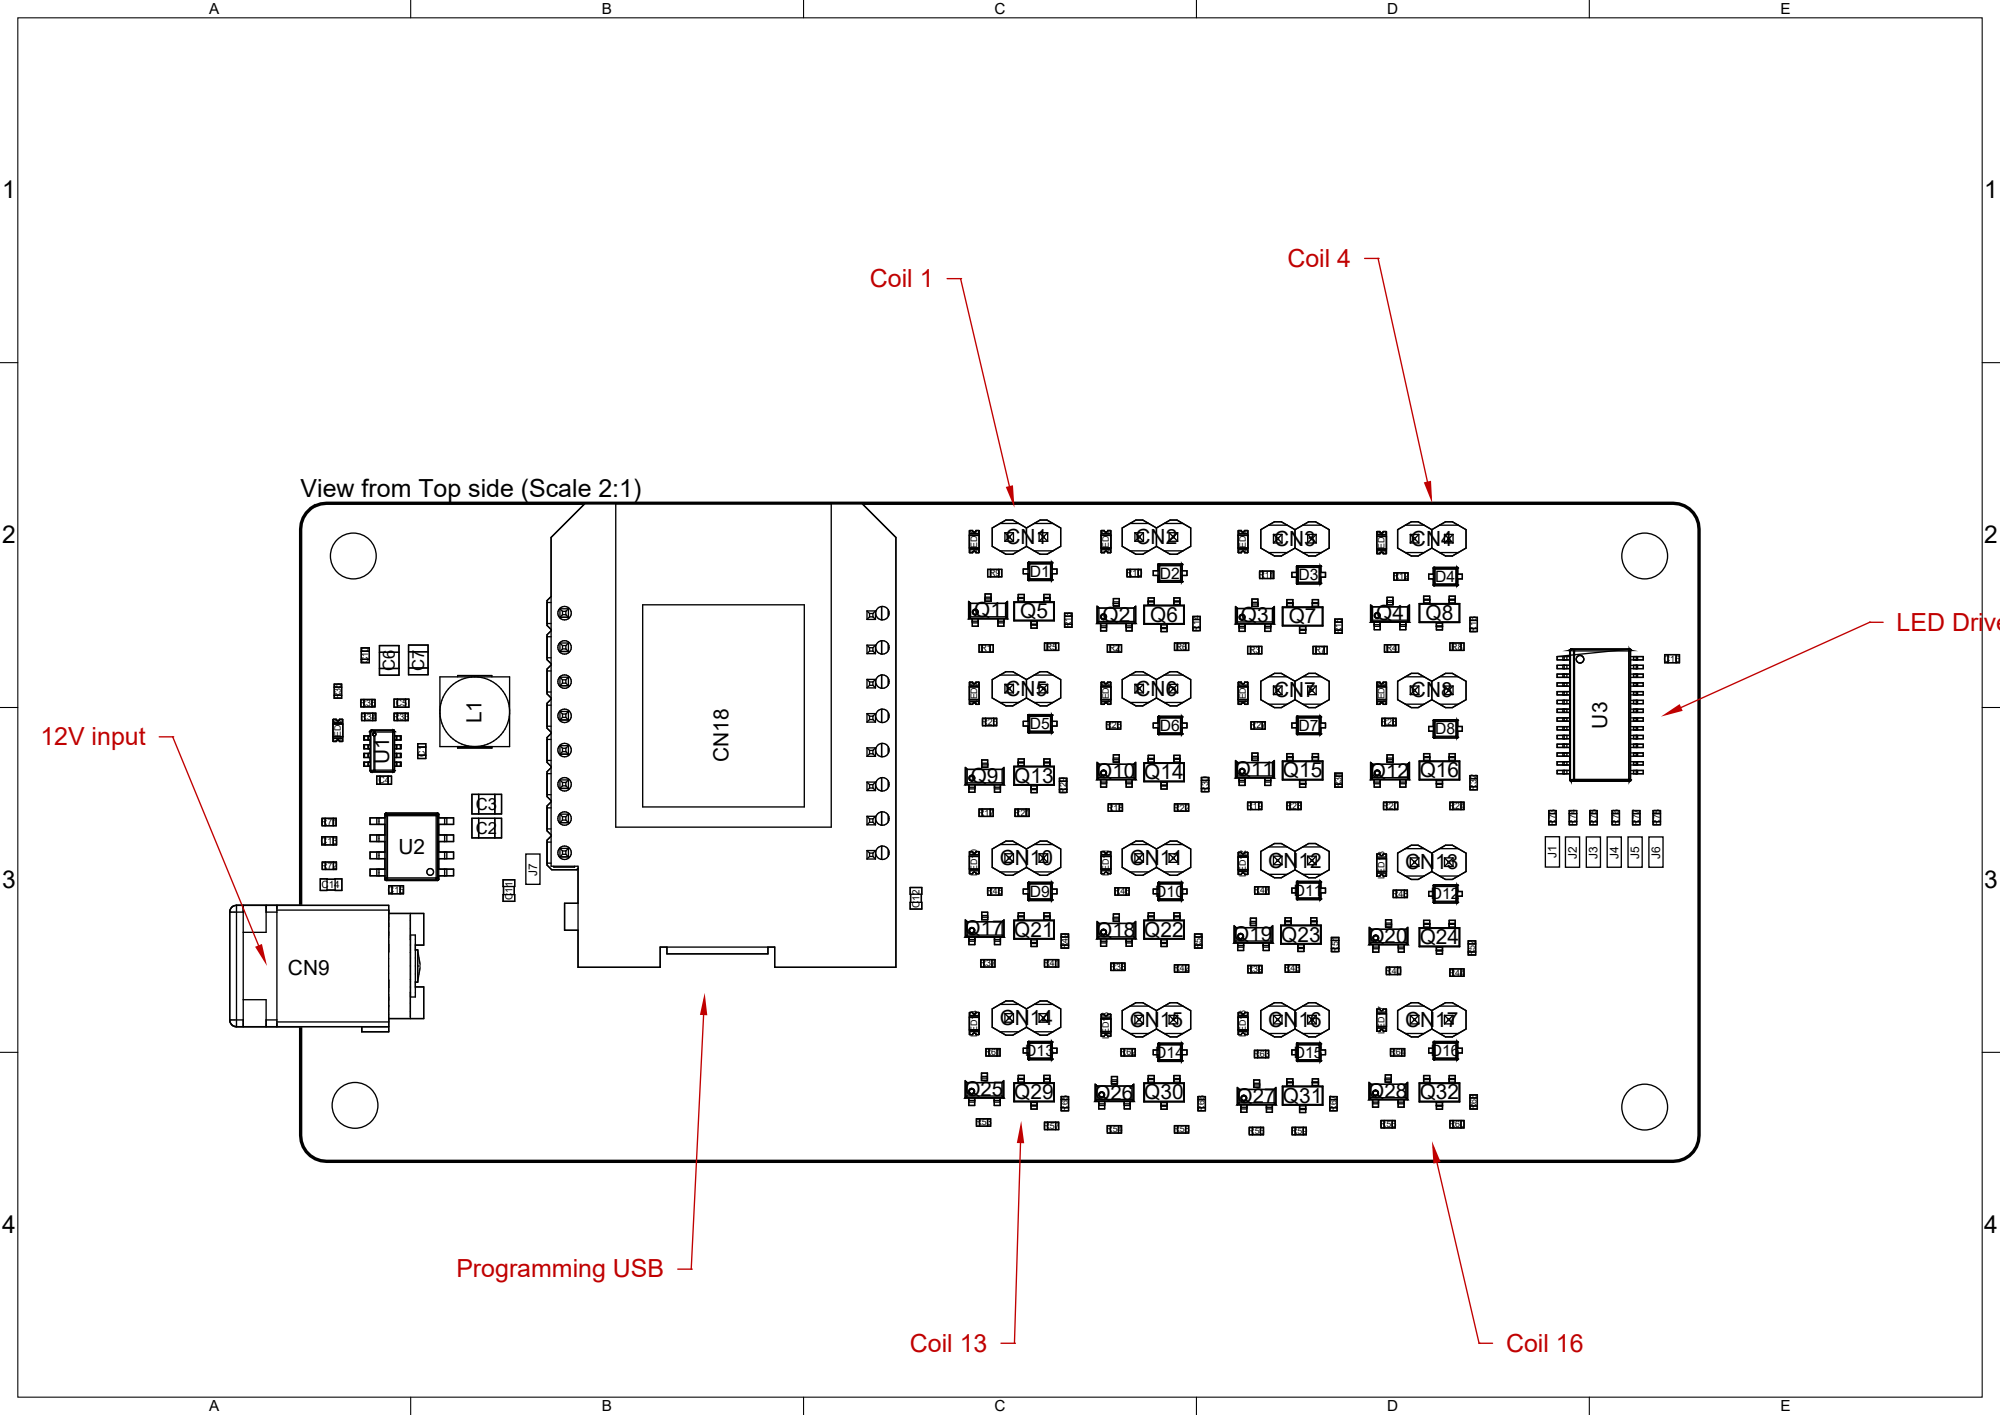
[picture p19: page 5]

View from Top side (Scale 2:1)
